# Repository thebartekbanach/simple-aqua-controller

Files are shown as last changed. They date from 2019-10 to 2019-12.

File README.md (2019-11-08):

# Simple aquaristic controller

### Language: **English** / [Polski](docs/pl/README.md)

## This project is a simple prototype of Aquaristic controller that supports automatic water change and automatic water addition from addional water tank.

## Main goals of this project:
- automatic water change basing on data coming from sensors
- half-automatic water change "add/remove"
- automatic water addition
- automatic water addition tank refill
- feeding mode
- operating accessories in the aquarium

## What will you need?
- basic knowledge about electrics and electronics
- soldering station
- knowledge about making a wires
- working 3D printer

# Gallery
## Front:
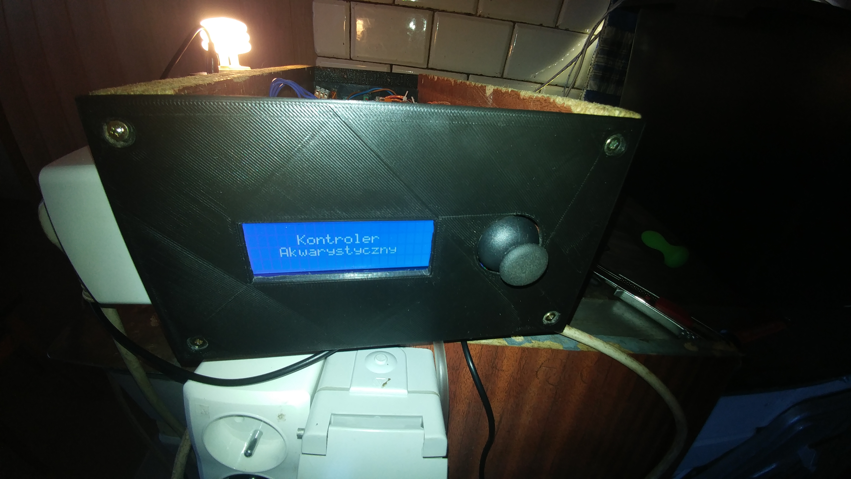
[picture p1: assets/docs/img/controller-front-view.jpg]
controller-front-view


## Side:
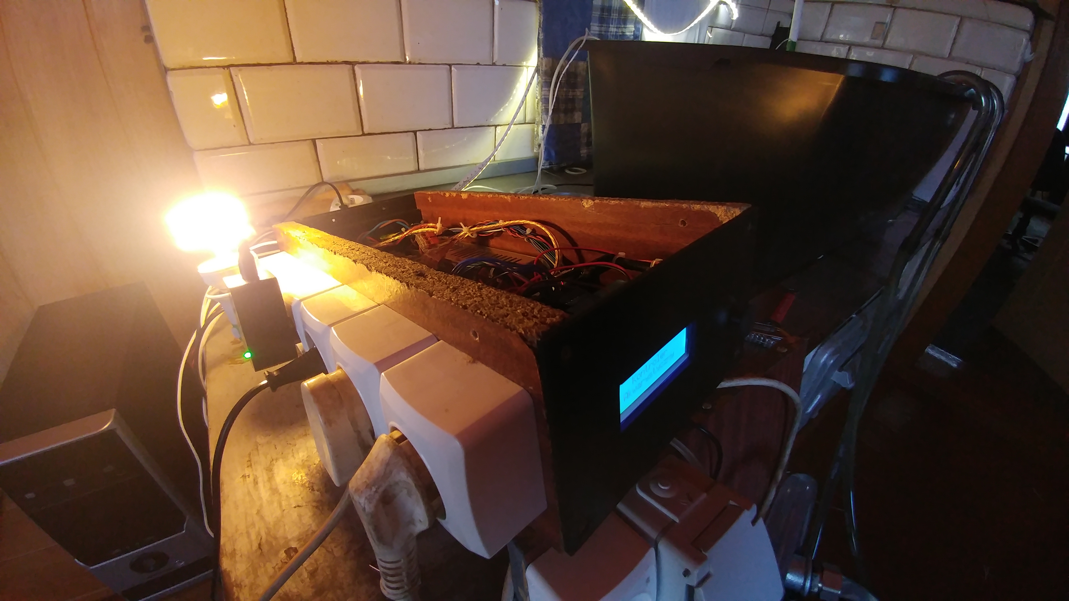
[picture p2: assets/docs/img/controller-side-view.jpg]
controller-side-view


## Back:
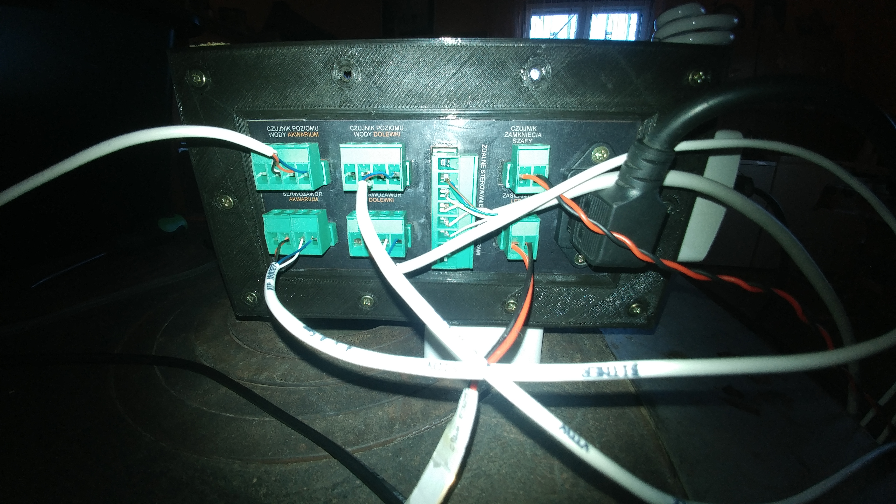
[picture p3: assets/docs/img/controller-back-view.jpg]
controller-back-view


## Inside:
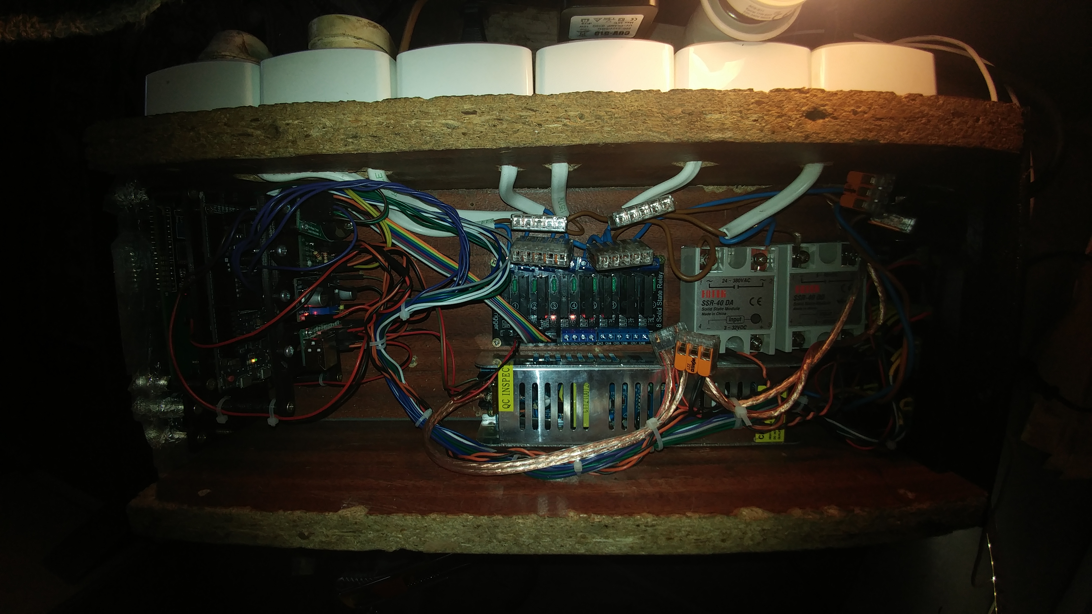
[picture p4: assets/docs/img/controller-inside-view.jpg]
controller-inside-view


# Hydraulics and pumps
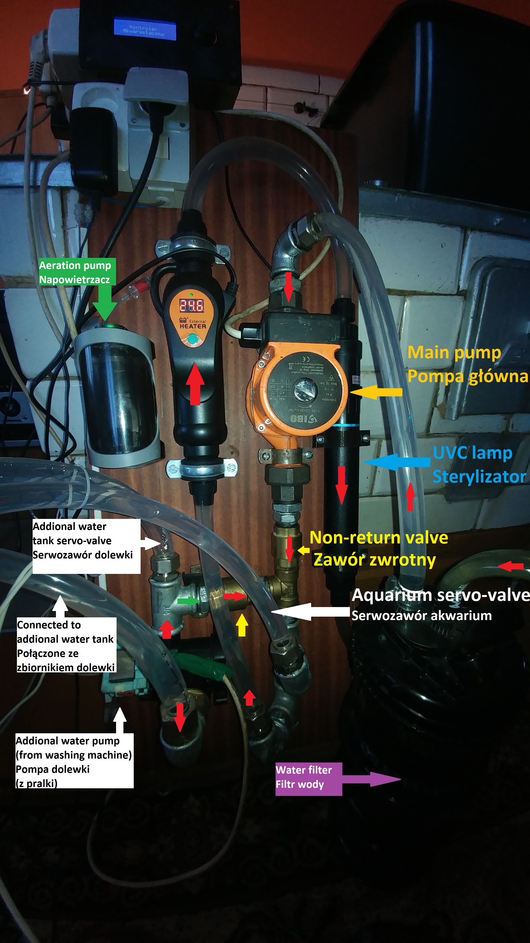
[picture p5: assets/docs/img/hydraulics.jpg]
hydraulics

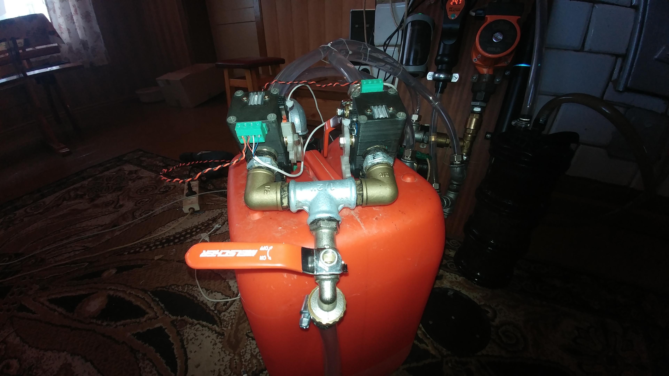
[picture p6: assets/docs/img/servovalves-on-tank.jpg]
servovalves-on-tank

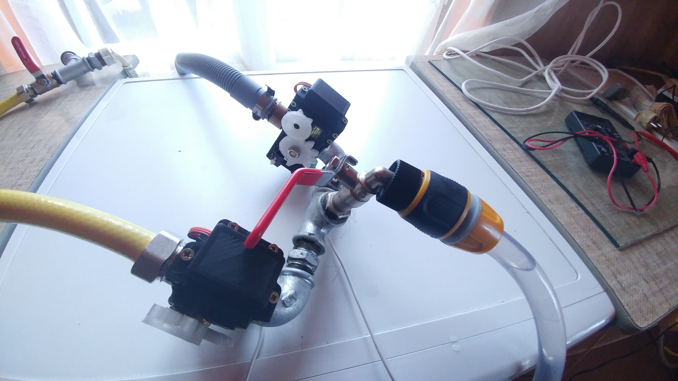
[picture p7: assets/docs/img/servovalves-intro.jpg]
servovalves-remote


## Requied hardware
- Arduino Due board
- `LCD 2004` screen with `HD44780` I2C converter
- `DS1302` RTC clock
- analog joystick like `KY-023`
- SSR relay module
- automatic water addition pump (from washer for example)
- four servovalves with close detection

# Servovalves
servovalves

## Why not solenoid valves?
Solenoid valves require pressure to operate.
When removing water from the aquarium using mainly gravity
we do not have enough pressure, so the use of solenoid valves falls off.
In addition, we use one hose here to inflow and outflow water from the aquarium.

## My own servovalves design
I have created my own servovalve design cheaper than servovalves from store.
3D printing knowledge is required to build them.
If you want to use another servovalves project you need to make
a fork of this project and implement your own interface
from `include/control/valves/valveModule.hpp`.

### Read more about servovalves [here](docs/en/servovalves.md).

# Water level sensors
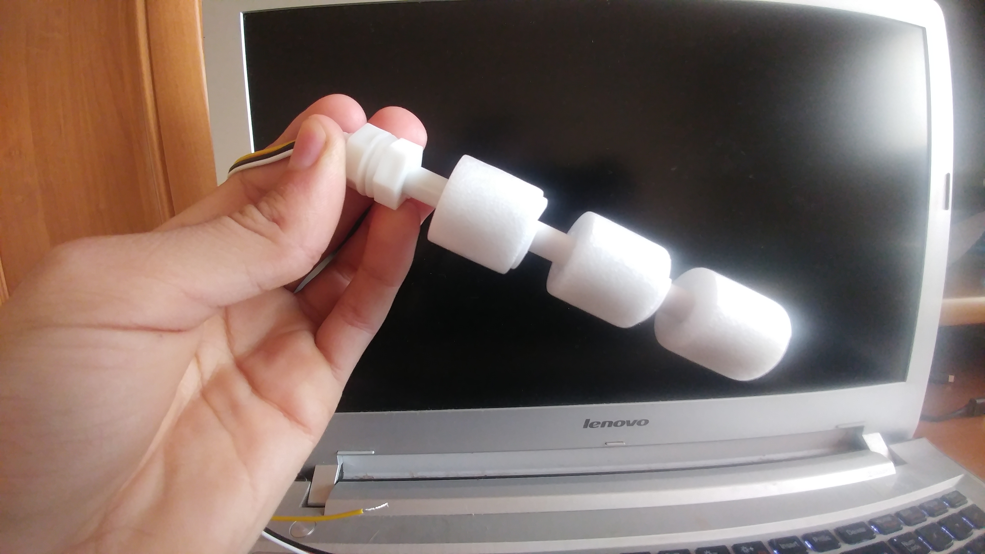
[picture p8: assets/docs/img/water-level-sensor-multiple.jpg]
water-level-sensor-multiple


## What can you use?
You can use what sensor you want. The only one
requirement is to conduct mass to arduino pin when
sensor detect water.

I know from experience that loose copper bare wires
as the electrodes of the water level sensor is not an ideal idea.
Unless the water level sensor is galvanically separated from
power sources just like industrial versions do.

## What am I using?
I use float sensors in my design,
because they are simple, cheap and effective.

### Read more about water level sensors [here](docs/en/water-level-sensors.md).

# The relays
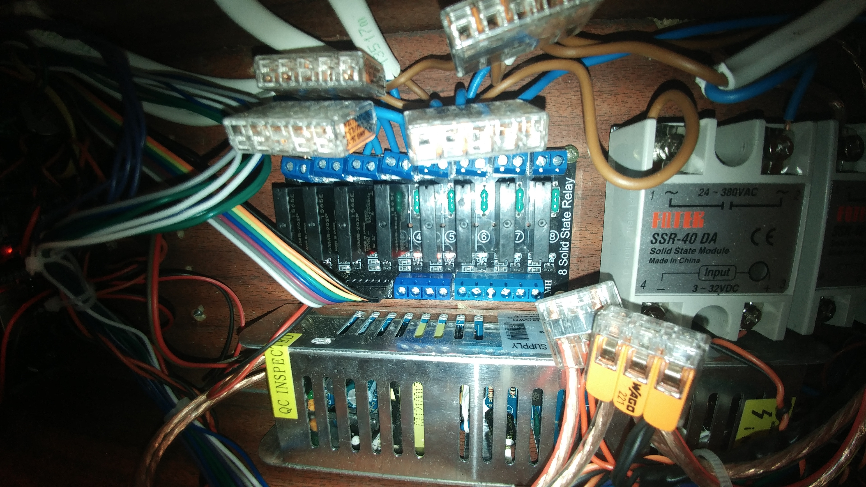
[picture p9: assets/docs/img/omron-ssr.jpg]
omron-ssr


## Why not mechanical relays?
Mechanical relays failed in my case.
In yours probably will not work too, and that's all
due to electromagnetic interferences that occurs
when switching. Partly it is the fault of the coils themselves,
partly it's the fault of the mechanical relays
do not switch at zero.

And Arduino is in no way protected against interference.

## Why SSR relays?
SSR relays have such an advantage over mechanical relays,
that they do not create electromagnetic interference. They are also more durable.
They have more energy losses, but for me it doesn't make much difference.

## Whose SSR relays?
It all depends on how power-hungry devices you connect.
The heater will probably be the most resource-consuming device.
I used an 8 channel SSR relay with `G3MB-202P OMRON` modules.
However, the maximum load capacity of these relays is only two amps.
So I had to buy a separate SSR relay `FOTEK SSR-40 DA 40A DC-AC`,
because my heater was too big for small OMRONs.

You may also need one more relay.

Remember that SSR modules intended for AC will not be
operate on DC current! Switching at zero blocks
the whole relay, since the DC current is direct current and there is no zero,
until you turn off the power.

So depending on the project you may need
a separate relay for LED strips.

### Read more about relays [here](docs/en/relays.md).

# How system works?
The system consists of 11 non-blocking
modules. Each module manages only its own part of the system.
For example: the `aerationControl` module only deals with
aeration management and the `lightControl` module takes care of
only aquarium lighting.

Each module has its own dependencies injected by the constructor.

And why manual injection? Because I did not think that C++ might have
working dependency injection system and I do not like to create
global variables.

### Read more about system [here](docs/en/system.md).

# Configuration
Configuration files are located here:
- screen: `include/control/screen/lcd.hpp`
- RTC clock: `include/control/rtc/configuration.hpp`
- relays: `include/control/relayModule/devices.hpp`
- water level sensors: `include/control/waterLevelSensor/devices.hpp`
- servovalves: `include/control/valves/devices.hpp`
- system modules: `include/modules/Modules.hpp`

# Installation
To upload this project you need the latest PlatformIO IDE.
Then connect the Arduino with a USB cable to the computer
and upload the project to the controller.

# First run
After the first start you need to check whether
everything has been connected properly.

## RTC clock
First make sure the RTC clock is
connected correctly. To do this, go to
`Main menu -> Settings -> Time and day cycle -> Current time`
and set the current time. Then disconnect the controller
completely from power and after a short while connect it on again.
If time has been preserved, we know
that the RTC clock has been connected correctly.

## Service mode
Then make sure to connect
sensors, devices and servo valves.
To activate the service mode, enter
`Main menu -> Settings -> Service mode`.
Then our eyes will see three main categories.
- `Sensors`: this category is for checking
correctness of connecting water level sensors.
- `Devices`: this category is used testing
the correctness of connecting relays, wiring and
the order of connecting the devices themselves.
- `Valves`: possibility to test servo valves.
We have five options here:
    - `Aquarium`: servo valve connected
    to main water circulation and filtering system in the aquarium
    - `Refill`: refill tank servo valve
    - `Clean water`: servo valve connected to the source of
    clean water from a tap or water pipe
    - `Sewage water`: servo valve for water outlet from aquarium
    - `Remote valves`: shows whether remote connection
    with servo valves is connected.

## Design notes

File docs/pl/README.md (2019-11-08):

# Prosty kontroler akwarystyczny

### Language: [English](../../README.md) / **Polski**

## Ten projekt jest prostym kontrolerem akwarystycznym z obsługą automatycznej podmiany wody i dolewki ze zbiornika rezerwowego.

## Główne cele tego projektu:
- automatyczna podmiana wody bazująca na czujnikach
- półautomatyczna podmiana wody "dolej/wylej"
- automatyczna dolewka wody ze zbiornika rezerwowego
- automatyczne uzupełnianie zbiornika dolewki
- tryb karmienia
- obsługa osprzętu w akwarium

## Czego potrzebujesz przede wszystkim?
- podstawowa wiedza na temat elektryki
- stacja lutownicza i wiedza jak jej użyć
- umiejętność zarabiania kabli
- sprawna drukarka 3D

# Kontroler
## Przód:
controller-front-view

## Bok:
controller-side-view

## Tył:
controller-back-view

## Środek:
controller-inside-view

# Hydraulika i pompy
hydraulics
servovalves-on-tank
servovalves-remote

# Potrzebny sprzęt:
- płytka Arduino Due
- wyświetlacz `LCD 2004` z konwerterem I2C `HD44780`
- zegar RTC `DS1302`
- analogowy joystick współpracujący z Arduino, np. `KY-023`
- płytka przekaźników SSR
- pompa automatycznej dolewki (np. nowa do pralki)
- cztery serwozawory z detekcją domyku

# Serwozawory
servovalves

## Czemu nie elektrozawory?
Elektrozawory wymagają ciśnienia do działania.
Podczas usuwania wody z akwarium za pomocą w głównej mierze grawitacji
nie mamy wystrczającego ciśnienia, więc użycie elektrozaworów odpada.
Poza tym, używamy tu jednego przewodu do wpływu i wypływu wody z akwarium.

## Własny projekt serwozaworów
Stworzyłem własny projekt serwozaworów tańszy niż serwozawory ze sklepów.
Całkowity koszt to jakieś 60 złotych za sztukę.
Do ich złożenia wymagana jest umiejętność użycia drukarki 3D.
Jeśli chcesz skorzystać z gotowych serwozawórów ze sklepu możesz zrobić forka
projektu i zaimplementować interfejs z pliku `include/control/valves/ValveModule.hpp`.

### Więcej na temat serwozaworów przeczytasz [tutaj](serwozawory.md).

# Czujniki poziomu wody
water-level-sensor-multiple

## Czego możesz użyć?
Możesz użyć czego chcesz. Wystarczy że gdy czujnik wykrywa wodę
poda na wybrany pin masę. Jeśli na pinie nie ma masy to znaczy
że czujnik nie wykrywa wody. Proste.

Z doświadczenia wiem, że zanużanie gołych miedzianych przewodów
jako elektrod czujnika poziomu wody nie jest idealnym pomysłem.
Chyba że czujnik poziomu wody jest separowany galwanicznie od
źródła zasilania, tak, jak robią to przemysłowe wersje.

## Czego ja używam?
Ja w swoim projekcie używam czujników pływakowych,
poniważ są proste, tanie, oraz skuteczne.

### Więcej na temat czujników poziomu wody przeczytasz [tutaj](czujniki-poziomu-wody.md).

# Przekaźniki
omron-ssr

## Dlaczego nie przekaźniki mechaniczne?
Przekaźniki mechaniczne nie dały rady w moim wypadku.
W Twoim prawdopodobnie też nie dadzą rady, a to wszystko ze
względu na zakłócenia elektromagnetyczne pojawiające się
podczas przełączania. Częściowo jest to wina samych cewek,
częściowo jest to wina tego, że przekaźniki mechaniczne
nie przełączają w zerze.

A Arduino w żaden sposób nie jest zabezpieczone przed zakłóceniami.

## Dlaczego przekaźniki SSR?
Przekaźniki SSR mają taką przewagę nad przekaźnikami mechanicznymi,
że nie tworzą zakłóceń elektromagnetycznych. Są też trwalsze.
Mają za to większe straty, ale jak dla mnie nie robi to wielkiej różnicy.

## Jakie przekaźniki SSR?
Wszystko zależy od tego jak prądożerne urządzenia będziesz podłączać.
Najbardziej zasobożernym urządzeniem będzie prawdopodobnie grzałka.
Ja użyłem 8 kanałowego przekaźnika SSR z modułami `G3MB-202P OMRON`.
Jednakże, maksymalna obciążalność tych przekaźników to tylko dwa ampery.
Musiałem dokupić oddzielny przekaźnik SSR `FOTEK SSR-40 DA 40A DC-AC`,
ponieważ moja grzałka była zbyt mocna dla małych OMRON'ów.

Możliwe że będziesz potrzebować jeszcze jednego przekaźnika.
Pamiętaj, że moduły SSR przeznaczone do AC nie będą
działać na prądzie DC! Przełączanie w zerze blokuje
cały przekaźnik, jako że prąd DC to prąd stały i nie ma zera,
dopóki nie odłączysz zasilania.

Więc w zależności od projektu, możesz potrzebować
oddzielnego przekaźnika dla taśm LED.

### Więcej na temat przekaźników przeczytasz [tutaj](przekazniki.md).

# Jak działa system?
System składa się z 11 nie blokujących głównego wątku
modułów. Każdy moduł zarządza tylko swoją częścią systemu.
Dla przykładu: moduł `aerationControl` zajmuje się tylko
zarządzaniem napowietrzaniem a moduł `lightControl` zajmuje
się tylko oświetleniem akwarium.

Każdy moduł ma własne zależności wstrzyknięte przez konstruktor.

A czemu ręczne wstrzykiwanie? Bo nie pomyślałem, że C++ może mieć
działający system wstrzykiwania zależności a nie lubię tworzyć
zmiennych globalnych.
 
### Więcej na temat systemu przeczytasz [tutaj](system.md).

# Konfiguracja
Pliki konfiguracyjne:
- wyświetlacz: `include/control/screen/lcd.hpp`
- zegar RTC: `include/control/rtc/configuration.hpp`
- przekaźniki: `include/control/relayModule/devices.hpp`
- czujniki poziomu wody: `include/control/waterLevelSensor/devices.hpp`
- serwozawory: `include/control/valves/devices.hpp`
- moduły systemowe: `include/modules/Modules.hpp`

# Instalacja
Aby zainstalować projekt potrzebne jest najnowsze PlatformIO IDE.
Potem podłączasz Arduino za pomocą kabla usb do komputera
i uploadujesz projekt na kontroler.

# Pierwsze uruchomienie
Po pierwszym uruchomieniu trzeba sprawdzić czy
wszystko zostało podłączone właściwie.

## Zegar RTC
Najpierw należy upewnić się że zegar RTC został
podłączony poprawnie. W tym celu należy się udać do
`Menu główne -> Ustawienia -> Czas i cykl dnia -> Aktualna godzina`
i ustawić aktualny czas. Następnie trzeba odłączyć kontroler
całkowicie od zasilania i włączyć ponownie.
Jeśli czas został zachowany to wiemy,
że zegar RTC został podłączony poprawnie.

## Tryb serwisowy
Następnie należy upewnić się co do podłączenia
sensorów, urządzeń i serwozaworów.
Aby aktywować tryb serwisowy, trzeba wejść w
`Menu główne -> Ustawienia -> Tryb serwisowy`.
Wtedy naszym oczom ukażą się trzy główne kategorie.
- `Sensory`: ta kategoria służy do sprawdzenia
poprawności podłączenia czujników poziomu wody.
- `Urządzenia`: ta kategoria służy przetestowaniu
poprawności podłączenia przekaźników, okablowania i
kolejności podłączenia samych urządzeń.
- `Zawory`: możliwość przetestowania serwozaworów.
Mamy tutaj cztery opcje:
    - `Akwarium`: serwozawór podłączony
    pod obieg wody w akwarium
    - `Dolewka`: serwozawór zbiornika dolewki
    - `Czysta woda`: serwozawór zapięty do źródła
    czystej wody, z kranu lub wodociągu
    - `Brudna woda`: serwozawór do wody ściekowej
    - `Zdalne zawory`: pokazuje czy zdalne połączenie
    z serwozaworami jest podpięte.

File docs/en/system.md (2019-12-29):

# System
The system consists of 11 non-blocking main threads
modules. Each module manages only its own part of the system.
Various basic implementations of base classes are included
in the file `include/system/SystemModule.hpp`.

# ArduinoMenu
The application uses the `ArduinoMenu` library to create and manage
and displaying the entire menu on the device display.

This is my [fork](https://github.com/thebartekbanach/ArduinoMenu/archive/master.zip)
of this library whose latest version can be found [here](https://github.com/neu-rah/ArduinoMenu).
Thanks for creating this library, [neu-rah](https://github.com/neu-rah)!

## Why fork and why did I have to change the original library?
Well, the original version of this library did not give opportunities
registering the event in the form of an indicator on the class method.
It is now possible with the `actionReceiver` class.
An example of use can be seen in the file
`include/system/ActionReceiver.hpp`.

# SystemModuleSettings
This is a template class as a template that adopts a structure of settings.
The main API consists of four main methods:
- `TSettings & data()`: returns the settings structure saved in memory
- `void saveSettings()`: this method should be called after changing the settings object in order to save them in the EEPROM
- `void resetSettings()`: resets settings to factory defaults,
that are given in the constructor
- `void restoreSettings()`: reads from EEPROM and overwrites
current settings, can be used to restore the edited values

# GlobalEventBus
This is the event bus used to send global events to
each module. Can be used to communicate between two
our modules. The best example of use can be a module
`TimeSetupModule` in the file
`include/modules/timeSetup/Module.hpp`.

It sends two events:
- `DAY_CYCLE_BEGIN` - start of the day
- `NIGHT_CYCLE_BEGIN` - the beginning of the night

# ActionCreator
This is the type of module that completely takes control
of the display and joystick. Can be used for
do something more advanced just like
`include/modules/feedingControl/FeedingActionCreator.hpp`

Before activating the action creator, make sure
that no creator is currently being executed.
An example of such a check can be found in the method
`void startFeedingModeEvent()` of the `FeedingControlModule` class
in the file `include/modules/feedingControl/Module.hpp`.

# TimeGuard
TimeGuard protects the RTC module against interference
and restarting time. When getting time all the time
from the RTC, TimeGuard module checks if the time is not older than
last measurement. If time is older, it means that
the clock restarted due to some external interference.
TimeGuard detects this and sets the RTC clock back to the last
known correct time.

This can cause the RTC clock to "slow down" if the controller is located
in an environment where interference often occurs.

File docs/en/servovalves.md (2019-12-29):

# DIY servo valves

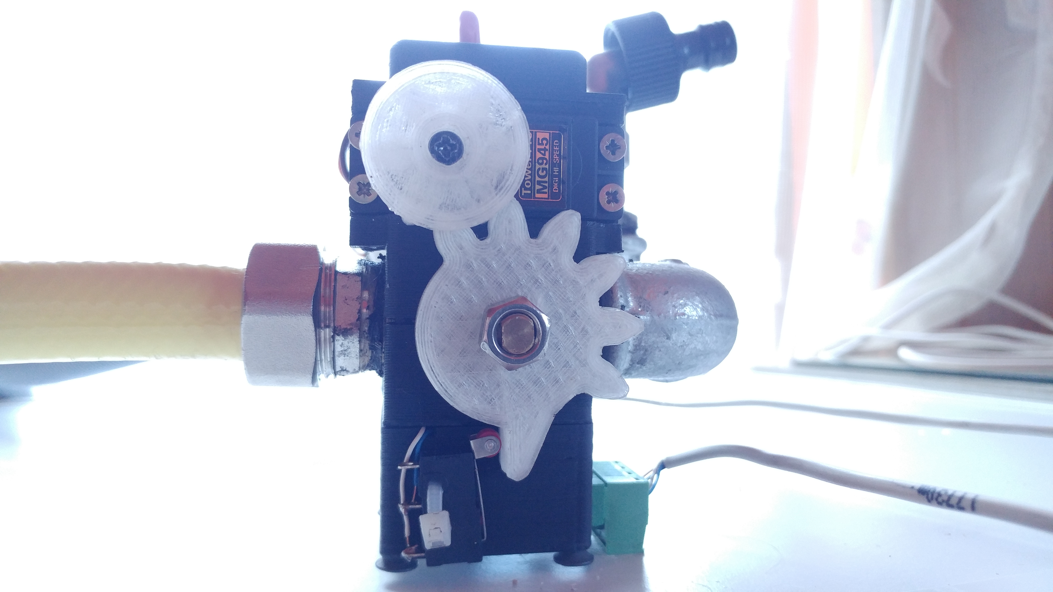
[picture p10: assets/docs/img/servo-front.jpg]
Servo-front

Servo-left
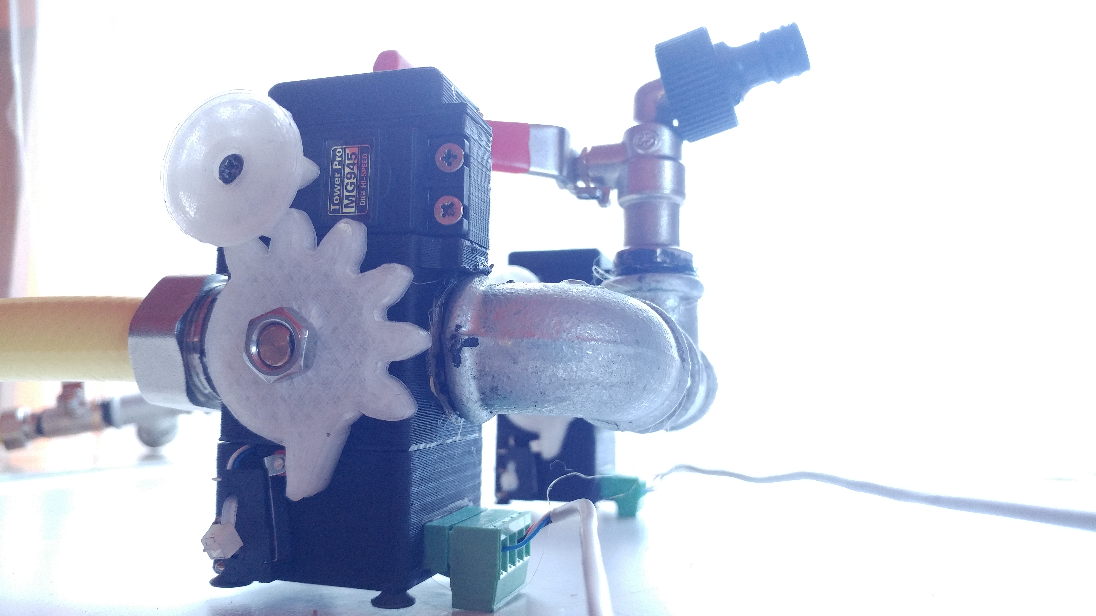
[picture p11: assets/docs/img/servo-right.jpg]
Servo-right

Servo-far-right
Servo-back
Servo-top

## What do you need to assemble servo valves?
- four servos in standard size, e.g. `TowerPro MG945`
- four ball valves
- four voltage regulators 5V or 6V,
- four heat sinks for voltage regulators
- four endstops
- four mounting strips 4-pin 5.08mm female + superglue for gluing them to 3D printed case
- four mounting strips 4-pin 5.08mm male
- some cables
- some filament for a 3D printer other than PLA

## How strong must the servos used in the project be?
My servos `TowerPro MG945` have a capacity of 10 kg per cm with 5V supply.
According to my observations, they are barely enough
for 1/2 inch ball valves. It's best to use a servo
with a higher load than those described above.
You should also remember about strong enough
voltage stabilizer and an appropriate heat sink.
My servo housing with PLA at the stabilizer heat sink
becomes soft after frequent switching
servo valves in a short period of time,
so I advise you to watch this too.

## STL files
STL files can be found in the folder
`assets/stl/servovalve`.

## Plug
1. Red: from + 6V to + 32V connected to a 5V voltage stabilizer, servo connected to a 5V voltage stabilizer output
2. Black: common ground for servo valve power supply and aquarium controller power supply
3. White: PWM control signal connected directly to the servo
4. Blue: endstop detecting servo valve closing, if enabled - conducts common ground, **not +5V or +12V!**

# API
The main interface of the servo valve driver is in the file
`include/control/valves/ValveModule.hpp`.

We have two instances of servo valve driver available:
1. `ValveModuleUsingInternalPwm` - this driver uses
    Arduino as a device generating PWM signal.
    The PWM outputs for this instance are configured in
    using pinout in the section `Valves servos pwm pinout definition`.
    The rest of the pinout is shared with the second driver.
2. `ValveModuleUsingExternalDriver` - this driver
    can be used in case of problems with the PWM generated
    by Arduino Due. I had to use it.
    This driver uses `Adafruit PWM Servo Driver`
    or any clone supported by the library
    `Adafruit PWM Servo Driver library`.
    Additional when using this module you don't need
    to worry about the configuration section
    `Valves servos pwm pinout definition`,
    it is not used when configuring this driver.

## The main API consists of five methods:
- `bool open(unsigned short valveId);`
- `bool close(unsigned short valveId);`
- `bool set(unsigned short valveId, bool state);`
- `bool isClosed(unsigned short valveId);`
- `bool areRemotesAvailable();`

Three blocking methods called `open`,` close` and `set`
are used to open and close servo valves.
As you can see, they return a boolean variable.
This is the result of executing the command.
If these methods return `true`, then
the controller knows that the servo valve did
command correctly. Otherwise, when `false` is returned,
the controller closes all servo valves and will show
information that there is a problem with servo valves
and you have to look at them and fix them.

The `isClosed` method, as the name suggests, returns
information about current status of the servo valve.
It reads this information from the endstop of
selected servo valve. If the endstop is closed
returns `true`, otherwise `false`.

The `areRemotesAvailable` method is a special method,
which should also be implemented
if the aquarium is not permanently attached to
source of clean water and sewage. It detects
if the remote servo valve control cable in another
room is connected to servo valves.
It can be e.g. a LAN cable in which one wire
is mass, next to are used for servo control
using the PWM signal, the next two are door detection
servo valves and the last one is detection
if remotes steering cable is connected.
It is shorted simply with mass.

remote-servovalve-connector

The current API works in such a way that the servo valve has 2-3 seconds to open
or close, if it does not do it in this time - an error is reported.

The main definition is in `include/control/valves/ValveModule.hpp`.
Individual implementations are in the same folder.

## ValveModuleBase
It's a class you can inherit. This is the base for the servo valve driver
with special functionality - disconnects the PWM signal of the servos after a specified time.
If we use ordinary servos in our servo valves, we can simply implement just
two protected methods and do not worry about automatic servo valves detach.

### Why disconnect the servo valve control signal?
Built in drivers in servos can cause servo buzzing
which means that the servo is trying to move to
selected position, even if it is missing just 0.1 degree,
so it doesn't use all the power of the servo and uses the engine
all the time but can't move to the end. It puts a load to the stabilizers,
so that they may not provide the required current to the servo at the required time,
which will cause a problem moving it to the selected position.

### Implementation:
To implement your own driver inheriting from `ValveModuleBase` you should
overwrite two protected, abstract methods:
- `void moveServo (unsigned short valveId, bool state);`
- `void detach (unsigned short valveId);`

The `moveServo` method is used to handle the movement of the servo - opening it or
closing depending on the value of the `bool state` argument.
It should not block the program execution.

The `detach` method is used to interrupt the PWM control signal feed
for servo. It is called after a set time. `ValveModuleBase` automatically
memorizes the last time the servo was moved and calls this method after timeout.

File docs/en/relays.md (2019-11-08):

# Relays

controller-inside-view

Solid state relays are very important
part of this project. You have to choose those that
will suit our needs.

The most important is to know what current
our devices will draw and selection of right SSR modules.

omron-ssr

In my case, almost all devices
could be served by relays
`G3MB-202P OMRON` whose maximum
the load is 2A which gives the maximum value
460W for one device. However, it is not worth approaching
to this value, so I suggest you hook up to
these relays up to 300W.

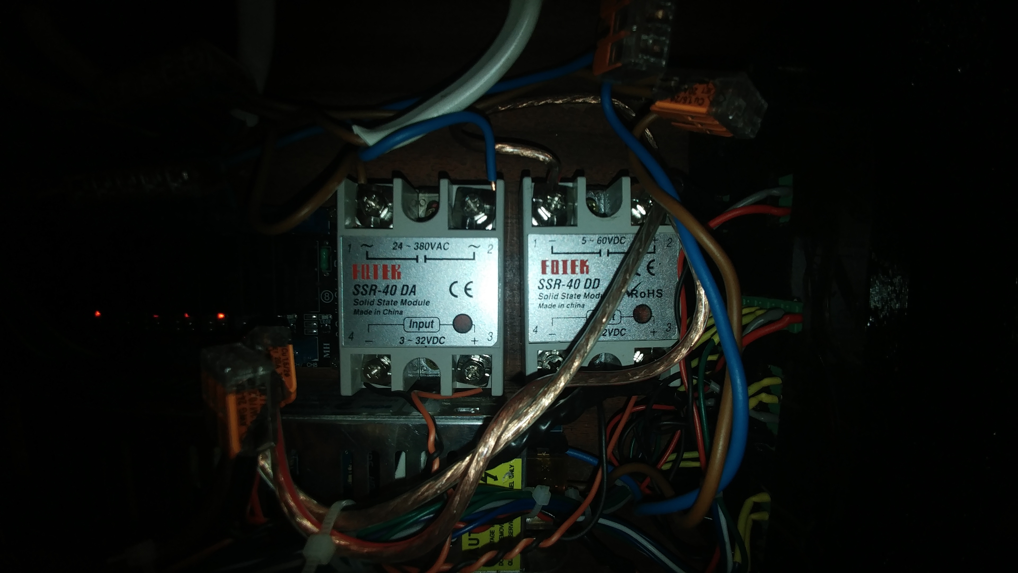
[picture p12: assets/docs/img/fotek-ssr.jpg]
fotek-ssr


The above pictures are showing two additional
SSR relays made by `Fotek`.

The first one of them is used for connecting a 500W heater.

The second one is SSR DC-DC type. It can switch
direct current. I use it to turn on the LED lighting,
because my Arduino is powered
from the same power supply as the LED lighting.

In addition, I gave the distance between the bottom of the `Fotek`
relays and the bottom of the controller to maintain better cooling.

**Remember that SSR modules intended for AC will not be
operate on DC current! Switching at zero blocks
the whole relay, since there is no zero crossing,
until you turn off the power.**

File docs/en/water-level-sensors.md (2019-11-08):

# Water level sensors

## I am using something like this:
water-level-sensor-white
water-level-sensor-black

## Connecting
Common cable connecting all switches
we connect to a common ground. Sensor outputs
connect to the Arduino inputs specified in the file
`include/control/waterLevelSensor/devices.hpp`.

## Testing
To test the correctness of connections, enter into
`Main menu -> Settings -> Service mode -> Sensors`
and then manually turn on each sensor and check that
it corresponds to the corresponding sensor in the controller.

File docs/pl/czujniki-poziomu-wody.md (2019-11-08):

# Czujniki poziomu wody

## Ja używam czegoś w tym rodzaju:
water-level-sensor-white
water-level-sensor-black

## Podłączenie
Wspólny przewód łączący wszystkie kontraktony
podłączamy pod wspólną masę. Wyjścia czujników
podpinamy pod wejścia Arduino podane w pliku
`include/control/waterLevelSensor/devices.hpp`.

## Testowanie
Aby przetestować poprawność połączeń należy wejść w
`Menu główne -> Ustawienia -> Tryb serwisowy -> Sensory`
a następnie ręcznie załączać każdy czujnik i sprawdzać czy
odpowiada on odpowiedniemu czujnikowi w kontrolerze.

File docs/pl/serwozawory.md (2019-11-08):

# Serwozawory DIY

servo-front
servo-left
servo-right
servo-far-right
servo-back
servo-top

## Czego potrzeba do złożenia serwozaworów?
- cztery serwa w rozmiarze standard, np. `TowerPro MG945`
- cztery zawory kulowe
- cztery stabilizatory napięcia na 5V,
- cztery radiatory do stabilizatorów napięć
- cztery krańcówki
- cztery listwy montażowe 4-pinowe raster 5.08mm żeńskie + superglue do ich wklejenia
- cztery listwy montażowe 4-pinowe raster 5.08mm męskie
- trochę kabli
- trochę filamentu do drukarki 3D, innego niż PLA

## Jak silne muszą być serwa użyte w projekcie?
Moje serwa `TowerPro MG945` mają udźwig 10 kg na cm przy zasilaniu 5V.
Z moich obserwacji wynika, że są one ledwo wystarczające
do zaworów kulowych 1/2 cala. Najlepiej użyć serw
z udźwigiem większym niż te które opisałem wyżej.
Należy również pamiętać o wystarczająco mocnym
stabilizatorze napięcia i odpowiednim radiatorze.
Moja obudowa serwozaworu z PLA przy radiatorze stabilizatora
staje się miękka po częstym przełączaniu
serwozaworów w krótkim okresie czasu,
tak więc na to również radzę uważać.

## Pliki STL
Pliki stl znajdziesz w folderze
`assets/stl/Servo-valve`.

## Wtyczka
1. Czerwony: od +6V do +32V podłączone do stabilizatora napięcia na 5V, serwo podłączone do wyjścia 5V stabilizatora napięcia
2. Czarny: wspólna masa zasilacza serwozaworu oraz zasilacza kontrolera akwarystycznego
3. Biały: sygnał sterujący PWM podłączony bezpośrednio do serwa
4. Niebieski: krańcówka wykrywająca domyk serwozaworu, jeśli jest załączona - przewodzi wspólną masę, **nie +5V albo +12V!**

# API
Główny interfejs sterownika serwozaworów znajduje się w pliku
`include/control/valves/ValveModule.hpp`.

Dostępne mamy dwie instancje sterownika serwozaworów:
1. `ValveModuleUsingInternalPwm` - ten sterownik używa
    Arduino jako urządzenie wytwarzające sygnał PWM.
    Wyjścia PWM dla tej instancji konfiguruje się za
    pomocą pinout w sekcji `Valves servos pwm pinout definition`.
    Reszta pinout jest wspólna z drugim sterownikiem.
2. `ValveModuleUsingExternalDriver` - tego sterownika
    można użyć w razie problemów z PWM'em generowanym
    przez Arduino Due. Ja musiałem go użyć.
    Ten sterownik używa `Adafruit PWM Servo Driver`
    lub jakiegokolwiek klona obsługiwanego przez bibliotekę
    `Adafruit PWM Servo Driver library`.
    Dodatkowa w przypadku użycia tego modułu nie trzeba
    się martwić sekcją konfiguracji
    `Valves servos pwm pinout definition`,
    nie jest ona używana przy konfiuracji tego sterownika.

## Główne API sterownika serwozaworów składa się z pięciu metod:
- `bool open(unsigned short valveId);`
- `bool close(unsigned short valveId);`
- `bool set(unsigned short valveId, bool state);`
- `bool isClosed(unsigned short valveId);`
- `bool areRemotesAvailable();`

Trzy blokujące metody o nazwach `open`, `close` i `set`
służą do otwierania oraz zamykania serwozaworów.
Jak widzisz, zwracają one zmienną typu boolean.
Jest to wynik wykonania polecenia.
Jeśli metody te zwrócą `true`, wtedy
sterownik wie, że serwozawór wykonał
polecenie poprawnie. W przeciwnym
wypadku, gdy zwrócony zostanie `false`,
sterownik zamyka wszystkie serwozawory
jakie tylko może i zwraca użytkownikowi
informację, że jest problem z serwozaworami
i trzeba się im przyjrzeć oraz naprawić je.

Metoda `isClosed` jak sama nazwa wskazuje zwraca
informację na temat aktualnego statusu serwozaworu.
Informację tę zczytuje z krańcówki domyku
wybranego serwozaworu. Jeśli krańcówka jest zamknięta
zwraca `true`, w przeciwnym wypadku `false`.

Metoda `areRemotesAvailable` jest metodą specjalną,
która również powinna zostać zaimplementowana
jeżeli akwarium nie jest podpięte na stałe do
źródła czystej wody oraz ścieku. Służy ona do
wykrycia, czy kabel sterujący serwozaworami w innym
pomieszczeniu został podpięty pod serwozawory.
Może to być np. kabel LAN, w którym jedna żyła
jest masą, dwie kolejne to sterowanie serwami za
pomocą sygnału PWM, dwie następne to detekcja domyku
serwozaworów a ostatnia żyła to właśnie detekcja
czy kabel jest podłączony dzięki spięciu masy do
detekcji podłączenia po stronie żeńskiej części
wtyczki LAN.

remote-servovalve-connector

Tak więc, podmieniając sterownik serwozaworów mamy możliwość
zgłoszenia błędów otwarcia i zamknięcia, które powodują przerwanie
aktualnie trwającego procesu i zamknięcie wszystkich otwartych serwozaworów.

Aktualne API działa w taki sposób, że serwozawór ma 2-3 sekundy na otwarcie
się lub zamknięcie, jeśli nie zrobi tego w tym czasie - zgłaszany jest błąd.

Główna definicja znajduje się w `include/control/valves/ValveModule.hpp`.
Poszczególne implementacje znajdują się w tym samym folderze.

## ValveModuleBase
Jest to klasa którą można odziedziczyć. Jest to baza sterownika serwozaworów
ze specjalną funkcjonalnością - odłącza sygnał PWM serwozawów po określonym czasie.
Jeśli używamy zwykłych serw w naszych serwozaworach to możemy po prostu zaimplementować
dwie chronione metody i nie martwić się automatycznym odłączaniem serwozaworów.

### Dlaczego warto odłączać sygnał serwozaworów?
Sterowniki wbudowane w serwa czasami powodują
buczenie ich, co oznacza że serwo próbuje przesunąć orczyk do
wybranego położenia, mimo że brakuje mu np. 0.1 stopnia,
przez co nie używa całej siły serwa i powoduje używanie silnika
przez cały czas. Bardzo nagrzewa to stabilizatory,
przez co mogą w wymaganym momencie nie podać wymaganego prądu do serwa,
co spowoduje problem z jego przesunięciem do wybranej pozycji.

### Implementacja:
Aby zaimplementować własny sterownik dziedzicząc z `ValveModuleBase` należy
nadpisać dwie chronione, abstrakcyjne metody:
- `void moveServo(unsigned short valveId, bool state);`
- `void detach(unsigned short valveId);`

Metoda `moveServo` służy do obsługi ruchu serwa - jego otwarcia lub
zamknięcia w zależności od wartości argumentu `bool state`.

Metoda `detach` służy do przerwania podawania sygnału sterującego PWM
do serwa. Jest wywoływana po ustalonym czasie. `ValveModuleBase` automatycznie
zapisuje ostatni czas poruszenia serwa i wywołuje tę metodę.

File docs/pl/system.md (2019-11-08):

# System
System składa się z 11 nie blokujących głównego wątku
modułów. Każdy moduł zarządza tylko swoją częścią systemu.
Różne podstawowe implementacje klas bazowych znajdują się
w pliku `include/system/SystemModule.hpp`.

# ArduinoMenu
Aplikacja używa biblioteki ArduinoMenu do tworzenia, zarządzania
i wyświetlania całego menu na wyświetlaczu urządzenia.

Jest to mój [fork](https://github.com/thebartekbanach/ArduinoMenu/archive/master.zip)
tej biblioteki której najnowszą wersję można znaleźć [tutaj](https://github.com/neu-rah/ArduinoMenu).
Dzięki za stworzenie tej biblioteki, [neu-rah](https://github.com/neu-rah)!

## Dlaczego fork i dlaczego musiałem zmienić oryginalną bibliotekę?
Otóż, oryginalna wersja tej biblioteki nie dawała możliwości
zarejestrowania eventu w postaci wskaźnika na metodę klasy.
Teraz jest to możliwe, za pomocą klasy `actionReceiver`.
Przykład użycia można zobaczyć w pliku
`include/system/ActionReceiver.hpp`.

# SystemModuleSettings
Jest to klasa szablonowa jako szablon przyjmująca strukturę ustawień.
Główne API składa się z czterech głównych metod:
- `TSettings& data()`: zwraca strukturę ustawień zapisaną w pamięci
- `void saveSettings()`: metodę tę należy wywołać po zmianie obiektu ustawień w celu zapisania ich w pamięci EEPROM
- `void resetSettings()`: restartuje ustawienia do fabrycznych,
czyli podanych w konstruktorze
- `void restoreSettings()`: wczytuje z pamięci EEPROM i nadpisuje
bieżące ustawienia, można użyć w celu przywrócenia edytowanych wartości

# GlobalEventBus
Jest to szyna zdarzeń służąca do wysyłania globalnych zdarzeń do
każdego modułu. Może posłużyć do komunikacji między dwoma
naszymi modułami. Najlepszym przykładem użycia może być moduł
`TimeSetupModule` znajdujący się w pliku
`include/modules/timeSetup/Module.hpp`.

Wysyła on głownie dwa eventy:
- `DAY_CYCLE_BEGIN` - początek dnia
- `NIGHT_CYCLE_BEGIN` - początek nocy

# ActionCreator
Jest to typ modułu który całkowicie przejmuje kontrolę
nad wyświetlaczem oraz joystickem. Może posłużyć do
zrobienia czegoś bardziej zaawansowanego.

Przykładem takiego kreatora akcji może być
`include/modules/feedingControl/FeedingActionCreator.hpp`

Przed aktywowaniem kreatora akcji należy upewnić się,
że żaden kreator nie jest aktualnie wykonywany.
Przykład takiego sprawdzenia znajduje się w metodzie
`void startFeedingModeEvent()` klasy `FeedingControlModule`
w pliku `include/modules/feedingControl/Module.hpp`.

# TimeGuard
TimeGuard jest zabezpieczeniem modułu RTC przed zakłóceniami
i restartowaniem czasu. Cały czas pobierając czas
z modułu RTC TimeGuard sprawdza, czy czas nie jest starszy względem
ostatniego pomiaru. Jeśli czas jest starszy, oznacza to, że
zegar zrestartował się pod wpływem jakiś zakłóceń z zewnątrz.
TimeGuard wykrywa to i ustawia zegar RTC ponownie do ostatniego
znanego poprawnego czasu.

Może to powodować "zwalnianie" zegara RTC jeśli kontroler znajduje
się w środowisku w którym często występują zakłócenia.

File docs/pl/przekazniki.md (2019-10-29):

# Przekaźniki

controller-inside-view

Przekaźniki półprzewodnikowe SSR są bardzo ważną
częścią tego projektu. Trzeba dobrać takie, które
będą odpowiadały naszym potrzebom.

Najważniejsza jest wiedza jaki prąd będą pobierać
nasze urządzenia i dobranie modułów SSR
z odpowiednim zapasem, gdyż chcemy, żeby nasze
urządzenie było chłodzone pasywnie, bez żadnych
wentylatorów.

omron-ssr

W moim wypadku prawie wszystkie urządzenia
mogły być obsłużone przez przekaźniki
`G3MB-202P OMRON` których maksymalne
obciążenie wynosi 2A co daje maksymalną wartość
460W na jedno urządzenie. Jednak nie warto zbliżać
się do tej wartości, więc sugeruję podpinać pod
te przekaźniki maksymalnie 300W.

fotek-ssr

Na powyższych zdjęciach widać również dwa dodatkowe
przekaźniki SSR od `Fotek`.

Pierwszy z nich służy mi do podłączenia grzałki 500W.

Drugi to SSR typu DC-DC. Może on przełączać
prąd stały. Używam go do załączania oświetlenia
ledowego, ponieważ moje Arduino jest zasilane
z tego samego zasilacza co oświetlenie ledowe.

Dodatkowo dałem dystanse między spodem przekaźników
`Fotek` a dnem kontrolera, żeby zachować lepsze chłodzenie.

**Pamiętaj, że moduły SSR przeznaczone do AC nie będą
działać na prądzie DC! Przełączanie w zerze blokuje
cały przekaźnik, jako że prąd DC to prąd stały i nie ma zera,
dopóki nie odłączysz zasilania.**

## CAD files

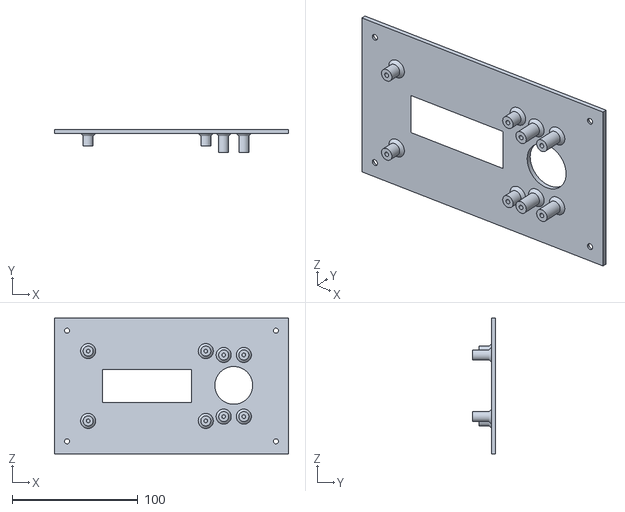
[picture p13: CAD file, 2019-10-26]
assets/stl/Controller-case/Front-cover.stl
186.0 x 18.0 x 108.0

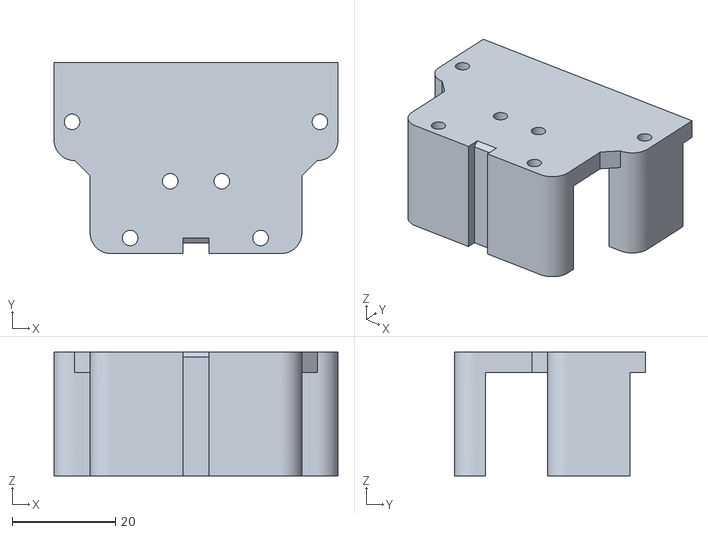
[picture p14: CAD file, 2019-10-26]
assets/stl/Servo-valve/Servo-mount.stl
55.0 x 37.0 x 24.0

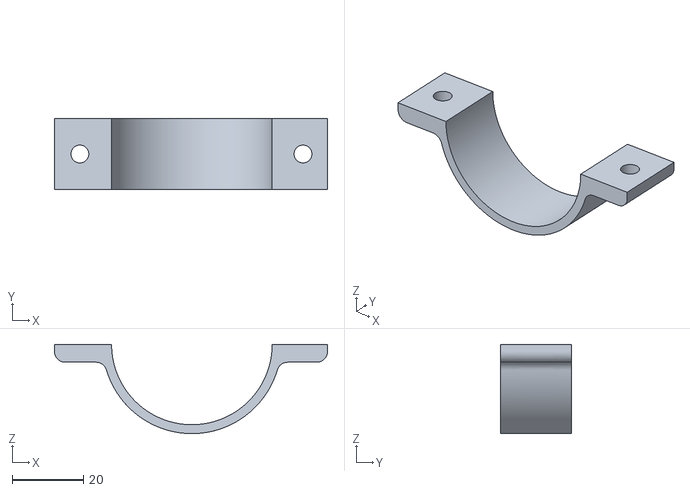
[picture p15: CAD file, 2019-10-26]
assets/stl/Sterilization-lamp-mount/Top.stl
76.5 x 20.0 x 25.0

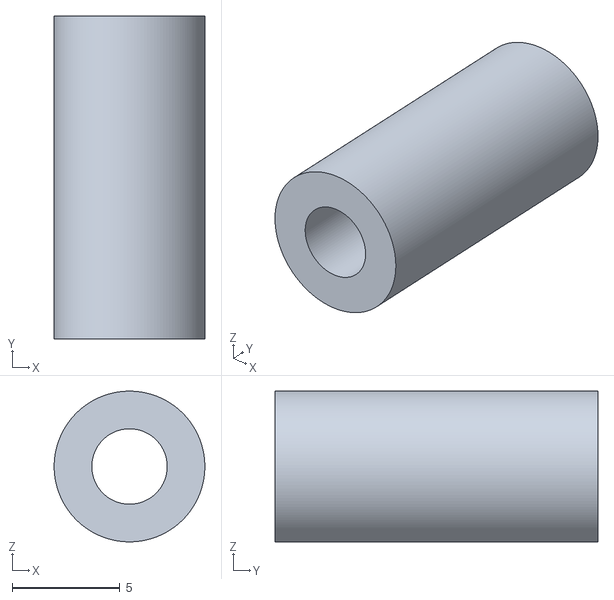
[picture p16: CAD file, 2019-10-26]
assets/stl/Controller-case/Arduino-mount-frame_screen-distance.stl
7.00 x 15.0 x 7.00

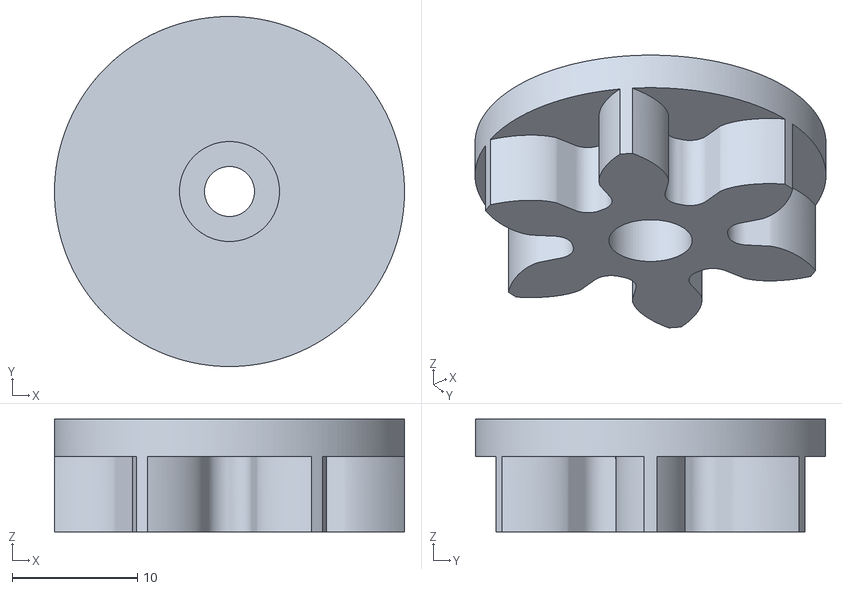
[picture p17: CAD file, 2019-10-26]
assets/stl/Servo-valve/Servo-gear-6.stl
28.0 x 28.0 x 9.00

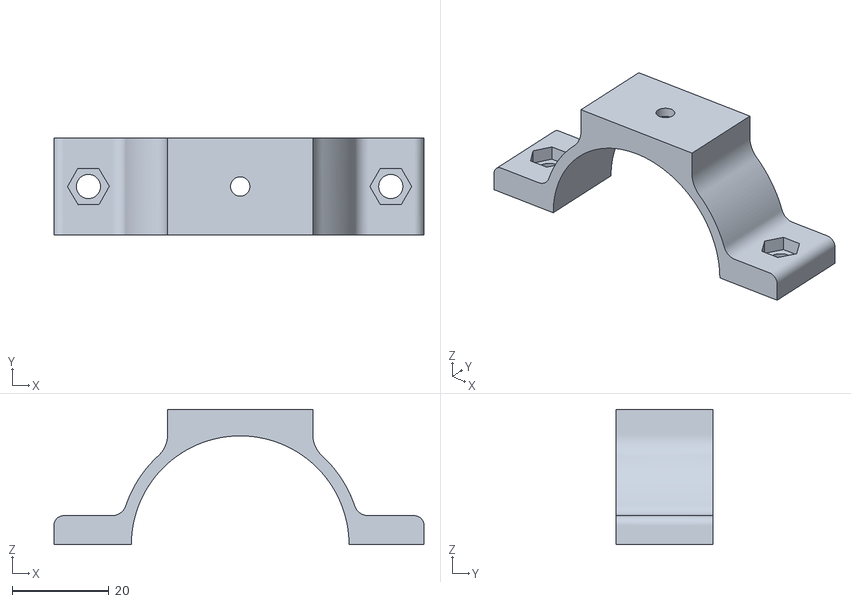
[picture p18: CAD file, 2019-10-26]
assets/stl/Sterilization-lamp-mount/Ground.stl
76.5 x 20.0 x 28.0

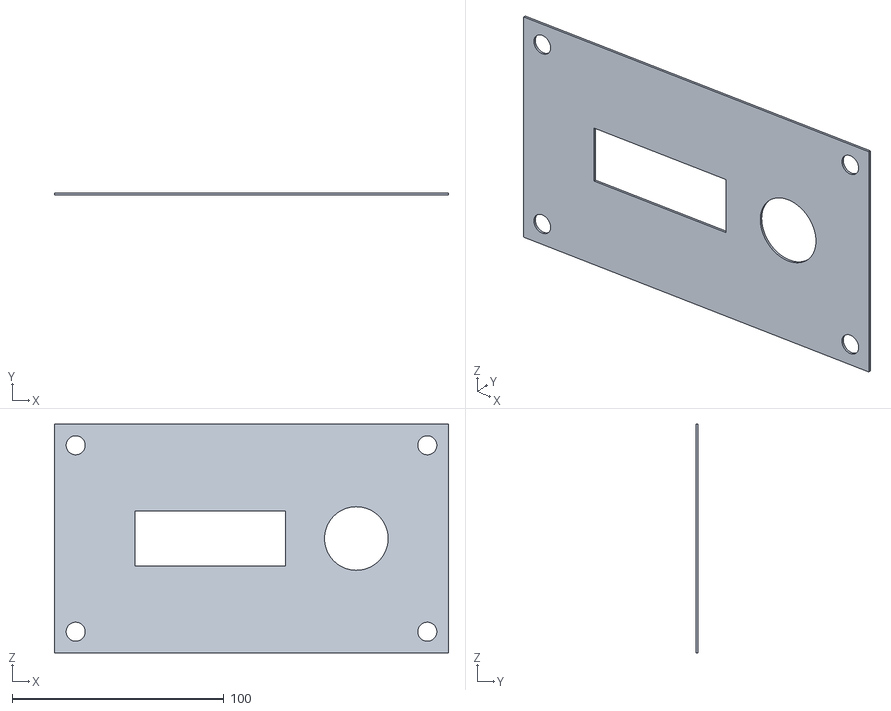
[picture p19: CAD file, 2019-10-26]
assets/stl/Controller-case/Front-cover-fix.stl
186.0 x 1.00 x 108.0

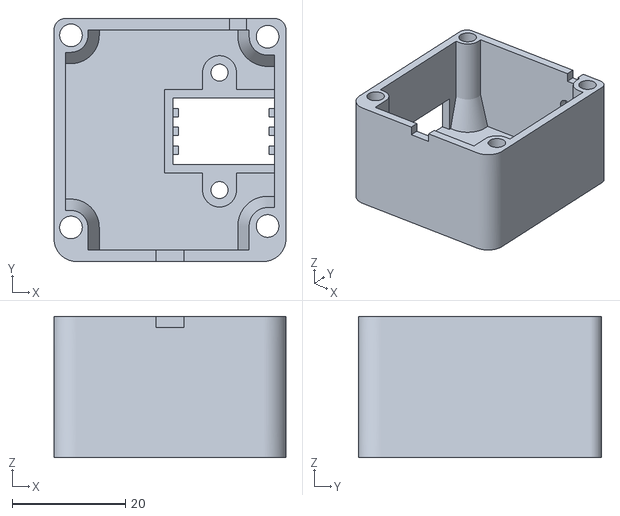
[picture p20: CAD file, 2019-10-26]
assets/stl/Servo-valve/Electronics-mount.stl
41.0 x 42.9 x 25.0

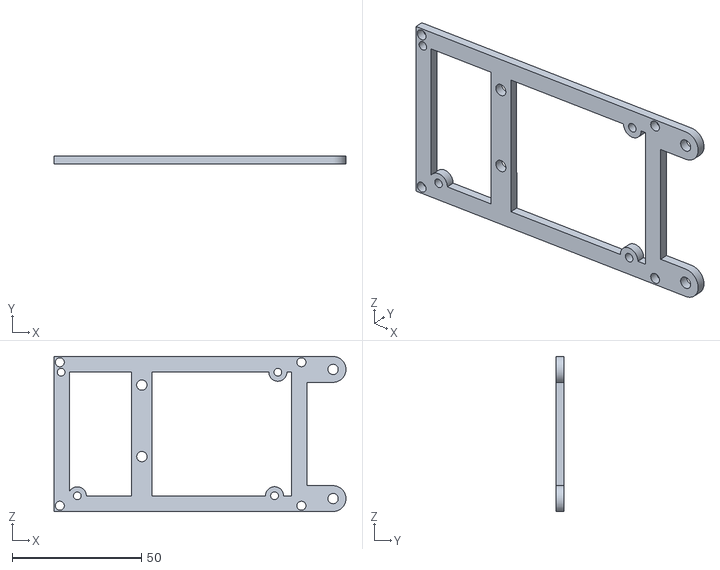
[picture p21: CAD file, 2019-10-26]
assets/stl/Controller-case/Arduino-mount-frame.stl
113.0 x 3.00 x 60.0

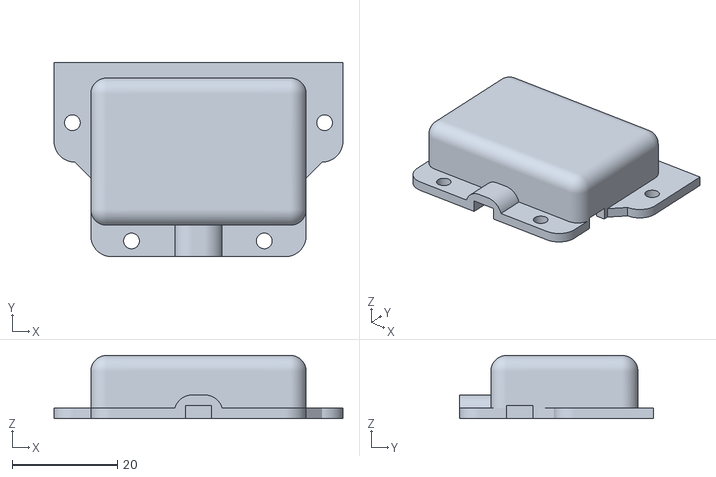
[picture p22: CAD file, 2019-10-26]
assets/stl/Servo-valve/Cable-cover.stl
55.0 x 37.0 x 12.0

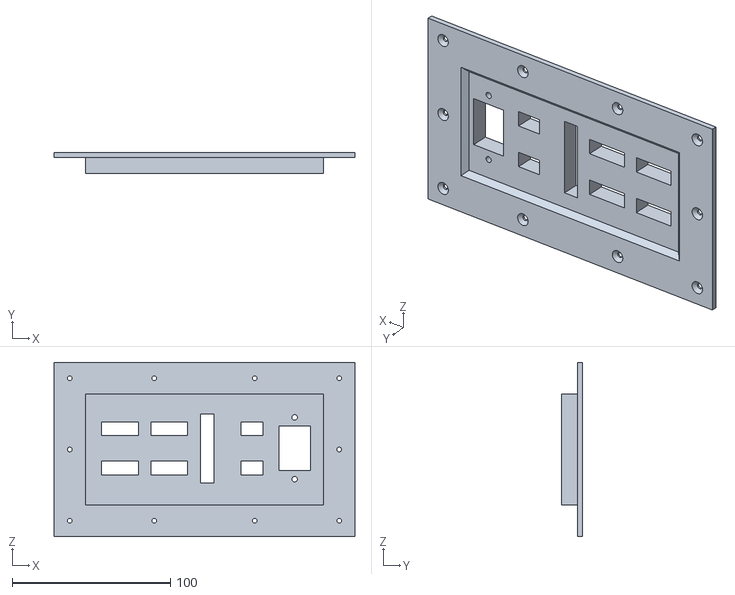
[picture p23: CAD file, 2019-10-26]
assets/stl/Controller-case/Backplate.stl
190.0 x 13.0 x 110.0

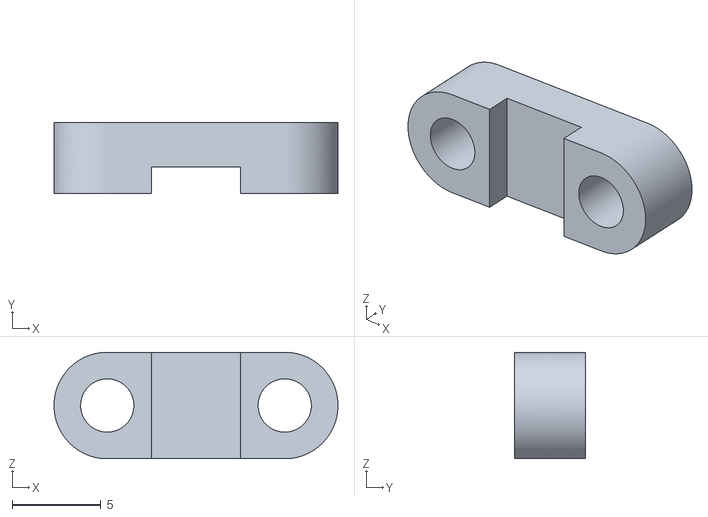
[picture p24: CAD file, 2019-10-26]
assets/stl/Servo-valve/Cable-holder.stl
16.0 x 4.00 x 6.00

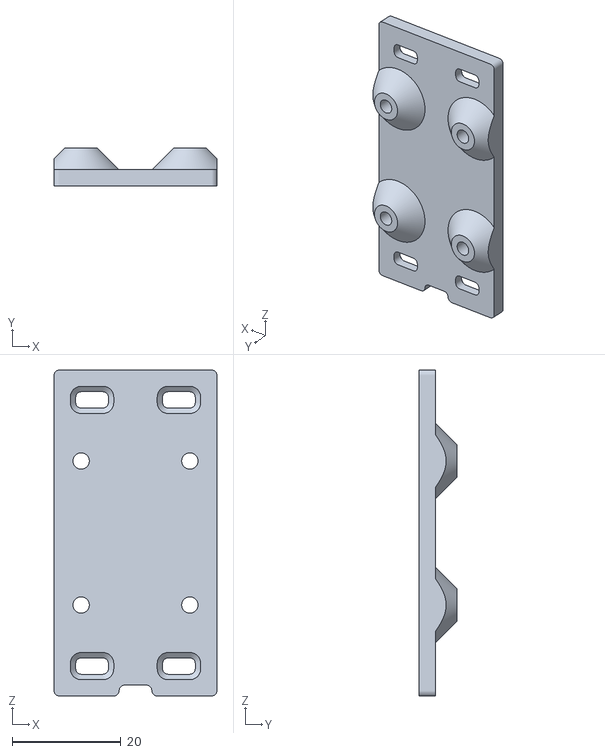
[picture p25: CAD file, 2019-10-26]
assets/stl/Controller-case/Joystick-mount.stl
30.0 x 7.00 x 60.0

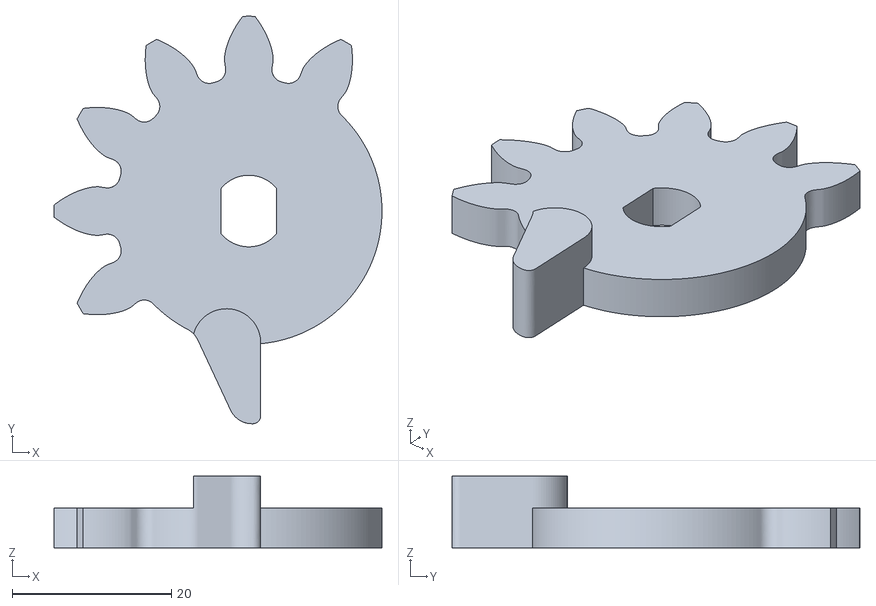
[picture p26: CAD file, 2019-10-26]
assets/stl/Servo-valve/Valve-gear-12.stl
41.2 x 51.2 x 9.00

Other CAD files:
assets/stl/Controller-case/Rtc-mount-on-addons-frame.stl
assets/stl/Servo-valve/Valve-body-connector-side.stl
assets/stl/Controller-case/Addons-frame.stl
assets/stl/Servo-valve/Power-converter-holder.stl
assets/stl/Controller-case/Addons-frame-distance.stl
assets/stl/Controller-case/Short-distance.stl
assets/stl/Servo-valve/Valve-body-servo-side.stl

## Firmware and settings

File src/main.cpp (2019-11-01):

#include <Arduino.h>

#define DEBUG_MODE_ENABLED
#include "utils/log.hpp"

#include "diagnostics/WaterLevelSensor.hpp"
#include "diagnostics/I2cScanner.hpp"
#include "diagnostics/Servos.hpp"
#include "diagnostics/AdafruitPwmServoDriver.hpp"

#ifndef DIAGNOSTICS_MODE

#include "program/Program.hpp"

Program* program;

void setup() 
{
    DEBUG_SERIAL_OUTPUT.begin(115200);

    logln("Enabling watchdog");
    watchdogEnable(8000);

    logln("Starting program...");
    program = new Program(); 

    logln("Starting setup...");
    program->setup();

    logln("Program started!");
}

void watchdogSetup() {
    // watchdog enable: https://forum.arduino.cc/index.php?topic=350058.msg2416416#msg2416416
}

void loop() 
{
    watchdogReset();
    program->update();
}

#endif

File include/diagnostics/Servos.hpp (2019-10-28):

#define SERVO_TEST_ENABLED false

#if SERVO_TEST_ENABLED == true
    #define DIAGNOSTICS_MODE

    #include <Arduino.h>
    #include <Servo.h>

    #include "../control/valves/devices.hpp"
    
    Servo aquarium;
    Servo addionalWaterTank;
    Servo cleanWater;
    Servo sewageWater;

    bool open = false;

	void setup()
	{
        aquarium.attach(AQUARIUM_WATER_VALVE_PIN);
        addionalWaterTank.attach(ADDIONAL_WATER_TANK_VALVE_PIN);
        cleanWater.attach(CLEAN_WATER_VALVE_PIN);
        sewageWater.attach(SEWAGE_WATER_VALVE_PIN);
    }

    void loop() 
    {
        aquarium.write(open ? SERVOS_OPEN_ANGLE : SERVOS_CLOSE_ANGLE);
        addionalWaterTank.write(open ? SERVOS_OPEN_ANGLE : SERVOS_CLOSE_ANGLE);
        cleanWater.write(open ? SERVOS_OPEN_ANGLE : SERVOS_CLOSE_ANGLE);
        sewageWater.write(open ? SERVOS_OPEN_ANGLE : SERVOS_CLOSE_ANGLE);

        open = !open;
        delay(2000);
    }

#endif

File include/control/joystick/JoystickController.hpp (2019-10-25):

#pragma once

#include <Arduino.h>
#include "JoystickActions.hpp"

#ifndef byte
    #define byte uint8_t
#endif

class JoystickController {
    private:
        const byte xPin;
        const byte yPin;
        const unsigned short moveDelayTime;

    public:
        JoystickController(const byte &xPin, const byte &yPin,
                        const unsigned short &moveDelayTime = (unsigned short)0):
            xPin(xPin), 
            yPin(yPin),
            moveDelayTime(moveDelayTime) {
                pinMode(xPin, INPUT);
                pinMode(yPin, INPUT);
        }

        JoystickActions collectActions() {
            int xVal = analogRead(this->xPin);
            int yVal = analogRead(this->yPin);

            JoystickActions action = NONE;
            
            if (yVal < 10) {
                action = UP;
            } else if (yVal > 1000) {
                action = DOWN;
            } else if (xVal > 1000) {
                action = BACK;
            } else if (xVal < 10) {
                action = OK;
            }

            if (action != NONE) {
                delay(moveDelayTime);
            }

            return action;
        }
};

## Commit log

2019-06-14 Add sample code with menu and joystick
2019-07-04 Add ActionReceiver for modified Arduino Menu library
2019-07-06 Fix ActionCreator support and add Timer class
2019-07-06 Change ArduinoMenu library dependency source
2019-07-08 Add relay module device controller
2019-07-09 Fix reversed joystick control
    [JoystickController.hpp]
2019-07-09 Fix device electromagnetic interference from relay module
2019-07-09 Add custom constructors and addional start methods overload to Timer class
2019-07-10 Add check if pin is alredy in requested state in RelayModule class
2019-07-11 Change main pump module id define name
2019-07-11 Add aeration, heather, lighting and sterilization control modules
2019-07-24 Add WaterLevelSensor devices definition
2019-08-02 Add valves devices definitions and registrations
2019-08-02 Change main pump module id definition name
2019-08-02 Update water level sensor devices pins
2019-08-05 Update relay module pinout
2019-08-06 Fix stateList array not initialized and shorter initialization time, rename turnedOnStates to turnedOffStates
    stateList array elements are all false after physical reset or sketch upload but after watchdog reset ram is not clean (00000) and it had random values that were causing weird devices behavior after watchdog reset
2019-08-06 Fix WaterAdditionControl pump switching loop when module water checking was not enabled (every update pump was turning off) and action creator was turning the pump on again
2019-08-08 Fix bad aquarium water valve pin
    [devices.hpp]
2019-08-09 Add water addition timer reset after change time settings
2019-09-30 Add servo library
2019-09-30 Fix joystick is not working after some changes in hardware
    [JoystickController.hpp]
2019-10-01 Many changes
    Add servo valves support
    Add I2cScanner diagnostics module
    Add heater module again
    Add ValveModule support in service module
    And many more
    TODO: debug every module with servo valves support
    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
2019-10-01 Fix "every device is on after startup"
2019-10-04 Fix interference-caused random valve errors
2019-10-04 Fix manual water change module strange valveModule pointer changes
2019-10-04 Add switch default statement and fix two spaces between displayed state string and state value
2019-10-06 Fix unnecessary servo write calls that causes servos jamming
2019-10-06 Improve user messages and add ConnectExternalWaterControl that requests user for remote servovalves connect and shows "done" button when everything is connected
2019-10-06 Add remote valves connection check service option
2019-10-13 Add safe precise timer
2019-10-13 Update ValveModule servo timing function to safe PreciseTimer
2019-10-13 Unify cancel buttons
2019-10-13 Fix slow timer usage in water addition module
2019-10-23 Add device enable/disable inherit api to TimeScopedDeviceDriver
2019-10-23 Add heater overheating safety lock
2019-10-23 Add heater overheat safety lock support to feeding control module
2019-10-23 Add heater overheat safety lock and turning off main pump when refilling aquarium
2019-10-23 Fix water addition does not stop after reaching max water level Fix too strong water pressure unables to add water by smaller pump Improve messages
2019-10-23 Update servo valve error messages text spacing
2019-10-23 Add hose pressure lowering action creator
2019-10-24 Add error message option for unknown valve
    [devices.hpp]
2019-10-24 Fix misleading error message when any valve is broken, now just message says that any valve is broken and you need to check that
2019-10-24 Fix cannot turn off main pump from another modules
2019-10-24 Add heater overheat safety lock support in manual water change
2019-10-24 Fix heater safety lock not working
2019-10-25 Add servo overheat protection for ValveModule
2019-10-25 Update servo valves configuration
2019-10-25 Move all action creators from valves/* into valves/actionCreators/*
2019-10-25 Fix intellisense errors caused by ushort word
    [JoystickController.hpp, devices.hpp]
2019-10-25 Fix unknown valve error
2019-10-25 Improve valves configuration readability
2019-10-25 Update water level sensors pinout definition and readability
2019-10-26 Add necessary stl's as assets
    [Addons-frame-distance.stl, Addons-frame.stl, Arduino-mount-frame.stl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]
2019-10-26 Add heating lamp control module and update constants and relay module initialization
2019-10-26 Move stl files to dedicated directory
    [Addons-frame-distance.stl, Addons-frame.stl, Arduino-mount-frame.stl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]
2019-10-28 Change servo move timeout and fix documentation
    [devices.hpp]
2019-10-30 Add heatingLamp service mode switch, fix order of class internals
2019-10-30 Change ValveModule to abstract base and inheriting module
2019-11-01 Add Adafruit PWM Servo Driver Library dependency
2019-11-02 Change valve open/close timeout, add Adafruit PWM Servo Driver module configuration
2019-11-02 Add external servo driver, improve ServoValvesStandbyControl
2019-11-02 Improve configuration of ValveModuleUsingExternalDriver
2019-11-08 Fix servo-valves control too quick servo disconnect
2019-11-08 Average emptying and refilling aquarium due to interferences on water level sensors
2019-11-08 Set Adafruit PWM Servo driver as a servovalve controller
2019-11-08 Avoid closing servovalves when next step will open the same valves again
2019-11-09 Add measurement averaging to WaterLevelSensor driver
2020-01-25 Rename ValveModuleUsingExternalDriver and add other constructor
2020-01-25 Add PwmLightController implementation using AdafruitPwmServoDriver
2020-01-31 Fix PwmLightControllerUsingAdafruitPwmServoDriver initialization
2020-01-31 Add PwmLightControllerUsingInternalPwm controller
2020-01-31 Change default heater device relay pin
2020-01-31 Change PwmLightController controller type
2020-02-08 Fix settings validation Some refactor Fix settings initialization Add settings validation and fix on day cycle change Fix driver frequency not reset after service mode leave
2020-02-08 Add servovalves service module
2020-02-10 Remove unecessary lighting relay setup
2020-02-10 Add RelayModuleServiceModule
2020-02-10 Add WaterLevelSensor and RelayModule service modules into ServiceMode
2020-02-10 Fix ServoValvesServiceModule not updating valve endstop info
